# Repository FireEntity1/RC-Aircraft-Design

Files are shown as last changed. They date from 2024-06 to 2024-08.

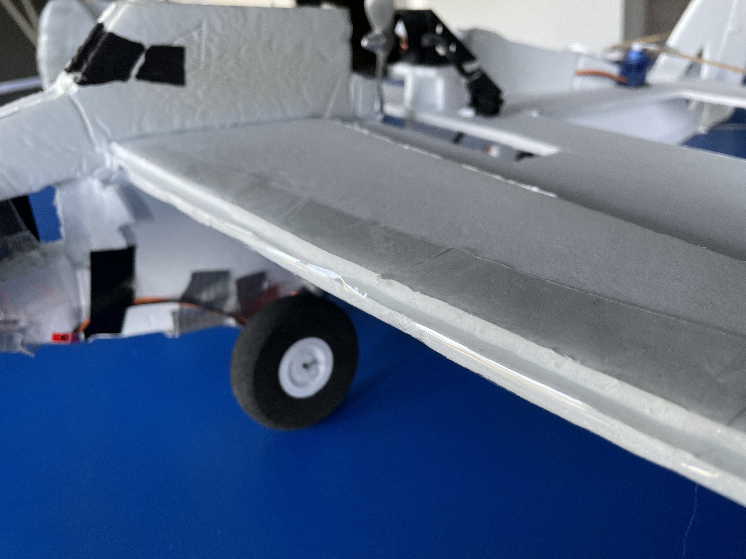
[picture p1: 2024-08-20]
design images/IMG_8348 2.JPG

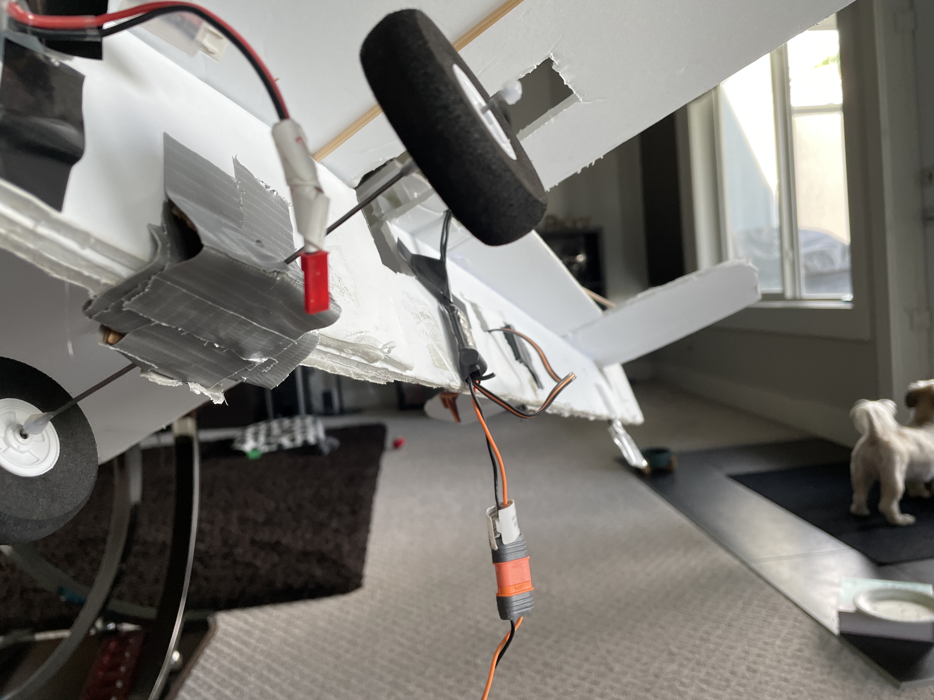
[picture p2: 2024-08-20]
design images/IMG_8361.jpeg

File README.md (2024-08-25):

I built a fully controllable, self propelled electric RC aircraft, capable of flying up to 80km/h (tested) at an altitude of several thousand feet (theoretical). The entire aircraft weighs a mere 250 grams so it's legal to fly without any license around the world! Flies smoothly with its 3 channel control system, consisting of throttle control, rudder control, and elevator control. The wings have a polyhedral design allowing the aircraft to stabilize itself laterally and remove the need for ailerons! An oversized rudder allows for precise control and "drifting" mid-air! The propeller, which is 6 inches in diameter with a 4 inch pitch is capable of spinning at 17 thousand RPM on a full battery, while the motor pulls ~40-50 watts. The aircraft is controlled with a 2.4gHz TX/RX system. Winglets (triangles on the wingtip) improve aerodynamic efficiency by reducing wingtip vorticies and add major style points! Fully decorated with decals, stripes, and a faux aircraft registration drawn on the body! The aircraft has a wingspan of nearly 3 feet.
Entering a deep stall is nearly impossible due to the nature of the aircraft, almost any mistake can be recovered if flown at a height of ~30-50 feet!

Built aircraft
Tail Section
Wingtip
Propeller closeup

Midflight:


https://github.com/user-attachments/assets/1de7d2b5-a0d6-459a-80c0-fe28b99d24c3

# Building it Yourself!:

To build your own RC aircraft similar to this one, download the pdf file labelled "plans" and print it out. On A4/Letter paper the drawing should be tiled to scale. Tape the plans together and cut out foamboard as the plans say!

### Ideal electronics:
 - 2204-size 2300kV brushless motor
 - 2x 9g servos
 - 2.4gHz transmitter/receiver
 - 2s/3s LiPo battery, 800-1200mAh
 - 15A speed controller (ESC)

### Build instructions
  - Screw the motor into anything light, thin, and sturdy, ideally a 3D printed mount, although a piece of wood with a hole drilled through it for the shaft would work as well. | Attatch the motor mount and propeller in the provided area outlined by the plans.
  - Attatch the servo arms to the control surfaces with control rods! | Servos should be taped or glued in with the arms being able to move fully
  - Make a tight area in the nose section of the aircraft for the battery, or on top. | Make sure it is protected as LiPos can be dangerous if punctured!
  - **Center of gravity should be 3.5-4 inches from the leading edge of the wing, this is extremely important, if your center of gravity is off, the aircraft will not fly**
  - Not much control surface throw (amount the control surfaces move) is needed, 15 degrees for rudder and elevator control each way should suffice.

  Once the aircraft is built and balanced, make sure the control surfaces move in the right direction. Pulling the elevator stick towards you should make the elevator on the aircraft tilt up, and vice versa. Moving the rudder stick to the right should make the rudder tilt to the right, and vice versa.

Test the aircraft with short flights and make adjustments as needed before taking it for a full flight, fly gently and do not make harsh movements on the control sticks

Decorate it as you please! Just remember to keep the weight low and not cover/damage sensitive electronics.

Thank you for reading and happy building!!

Feel free to reach out with any questions regarding construction or flight!

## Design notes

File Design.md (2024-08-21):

RC PLANE ---

High wing design
All-Up-Weight ~250 grams

Wingspan 32"
Fuselage 26"
Wingchord 7"
KFM-Step Airfoil

3 Channel Rudder-Elevator-Throttle design
Polyhedral wing for lateral stability
NO AILERON

2300kV Brushless Motor
2s LiPo
2x 9G servo
2.4gHz TX/RX
6*4 Inch Propellor
Approx ~300g of Thrust @ 8.4v

Taildragger landing gear
Middle mounted propellor

Winglet for wingtip vortex reduction

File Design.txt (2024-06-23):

RC PLANE ---

High wing design
All-Up-Weight ~250 grams

Wingspan 36"
Fuselage 24"
Wingchord 6"
KFM-Step Airfoil

3 Channel Rudder-Elevator-Throttle design
Polyhedral wing for lateral stability
NO AILERON

2300kV Brushless Motor
2s LiPo
2x 9G servo
2.4gHz TX/RX
6*4 Inch Propellor
Approx ~300g of Thrust @ 8.4v

Tricycle landing gear
Front mounted propellor

Winglet for wingtip vortex reduction

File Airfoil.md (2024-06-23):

FLAT PLATE
Stall Speed @5 degrees: 16km/h: 
Stall Angle @ 30km/h: Approx +23.3 degrees

CURVED (Under-cambered) PLATE
Stall Speed: 10km/h:
Stall Angle @ 30km/h: Approx. 24 degrees

An increase of camber results in increased lift capability at an increase of drag and reduce of structural integrity

No camber (flat bottomed) airfoil is ideal for simple construction, speed, and integrity at the cost of a higher stall speed.

Electronics will be housed inside the aircraft to minimize turbulent airflow, especially over wing and tail sections.

Airfoil design: Kline-Foglemen-2 Step Airfoil @ 50% Camber

Flight Characteristics: Slow-Medium speed, stall speed low

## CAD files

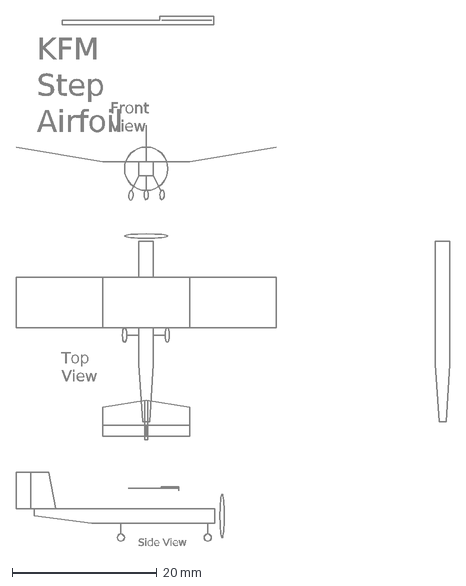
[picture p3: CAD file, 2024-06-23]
RC PLANE.dxf
KFM Step Airfoil
Front View
Top View
Side View

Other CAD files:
Airfoil.blend

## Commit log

2024-08-20 Revamp main gear + aerodynamic wings
2024-08-20 Winglets, tail gear, improved main gear
2024-08-20 Neater wires
2024-08-20 Gear modif., testing, deco, smooth surfaces
